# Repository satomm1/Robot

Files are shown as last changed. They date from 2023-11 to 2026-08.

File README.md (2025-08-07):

# Mobile Robot
This repository contains many instructions for setting up and constructing the robot. However, for a comprehensive guide, please visit: [https://satomm1.github.io/mattbot/instructions.html](https://satomm1.github.io/mattbot/index.html).

## Authors
Matthew Sato and Kincho Law<br>
satomm@stanford.edu<br>
Stanford University Department of Civil and Environmental Engineering<br>
Engineering Informatics Lab

## Description
This repo contains mechanical (CAD) designs, electrical schematics, and software for creating a wheeled mobile robot.

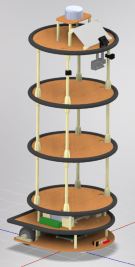
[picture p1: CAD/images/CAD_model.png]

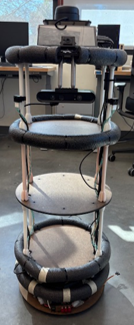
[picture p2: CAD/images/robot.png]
Mobile Robot


- The mechanical design is provided in the `./CAD` directory. In this directory, you will find [detailed instructions](./CAD/README.md) for constructing the mobile robot along with relevant STL/DXF files and a bill of materials. The CAD files were generated in Inventor.
- The electrical design for the various components are located in the `./Electrical` directory. In this directory, you will find electrical schematics and the PCB design for the main control board, IMU breakout board, microphone breakout board, and microphone controller board. A [detailed list of the components and instructions](./Electrical/README.md) for each of these boards is included.
- The software design for the main control board is in the `./Software` directory. This software is for the PIC32 located on the main control board and facilitates communication between the PIC32 and Jetson, performs PID control, odometry, etc. Additionally, the software for the microphone control board is included in this directory. Please visit the [README](./Software/README.md) for more detailed instructions.
- Instructions for the Nvidia Jetson Orin Nano aare provided in the `./Jetson` directory. This directory includes instructions for bringing up the Jetson, setting up the WiFi mesh node connectivity, setting up the Docker environments, and setting up the ROS environment/software stack. Please visit the [Jetson README](./Jetson/README.md) for more details.

## License

This project is licensed under the MIT License - see the [LICENSE](LICENSE) file for details.

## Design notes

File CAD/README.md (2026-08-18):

# CAD

This directory contains the CAD files for the mobile robot. The components for all parts are modeled with Autodesk Inventor and are available in the `Inventor` directory. An older version of the mobile robot design in SolidWorks is available in the `mechanical` zip file.

The remainder of this README provides instructions for creating the mechanical form of the mobile robot for the approximately 1 meter tall robot:

<p align="center">

Mobile Robot CAD Model
Real Mobile Robot
</p>

A comprehensive parts list is located in `BOM.xlsx` that will be needed for constructing this mobile robot.

1) **Laser cut the platforms out of a thin, stiff wood.** I use tempered hardwood (Duron) of 1/8"-1/4" thickness. Every file that should be laser cut is listed in the [Laser_Cuts.md](./Laser_Cuts.md) file. The corresponding DXF files needed for laser cutting are located in the [./dxf](./dxf) directory. For reference, to make sure the files are the correct size/units, the diameter of the circular platforms is 354 mm (14 inches).
2) **Prepare the 3D printed parts.** 3D Print the required parts using PLA plastic. Every file that should be 3D printed is listed in the [3D_prints.md](./3D_prints.md) file. The corresponding STL files are located in the [./stl](./stl/) directory. To verify that the 3D printed parts are the correct size/units, the length of the bearing blocks should be 3 inches (76 mm).

> [!NOTE]
> If you use different components (motor, wheels, etc), the laser cut or 3D printed files may need to be modified first. 

> [!IMPORTANT]
> The height of the motor holders and bearing blocks must be adjusted so that the bottom of the wheels are in plane with the ball casters. Adjust the hardboard_thickness in `Inventor/parameters.xlsx` and update the Inventor model. Verify everything is correct and re-export the motor holders and bearing block stl files.

> [!IMPORTANT]
> You should print the correct bearing block depending on whether your ball bearings have flanges. If the bearings don't have flanges, 3D print the bearing block designated with "no_flange."

3) **Insert heat set inserts.** Use a soldering iron to insert the heat set inserts into any 3D printed part that requires heat set inserts. The small end of the heat  set insert should enter the 3D printed part first. I recommend using a low temperature (~400F or 200C). 

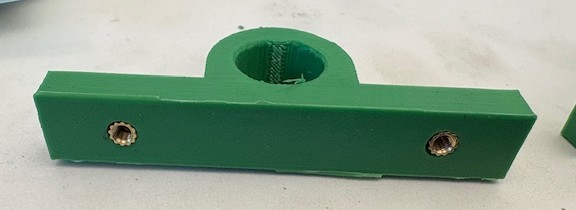
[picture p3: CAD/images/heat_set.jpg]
Heat set inserts


> [!TIP]
> IF you are not familiar with installing heat set inserts, watch this quick video: https://youtu.be/P7nHyI1TwKY?t=189.

4) **Install the motors.** Insert the motors into the motor blocks and secure with screws. **Important**: select the proper length screw (not too long!!!) so that the screw does not go too far and break the motor.

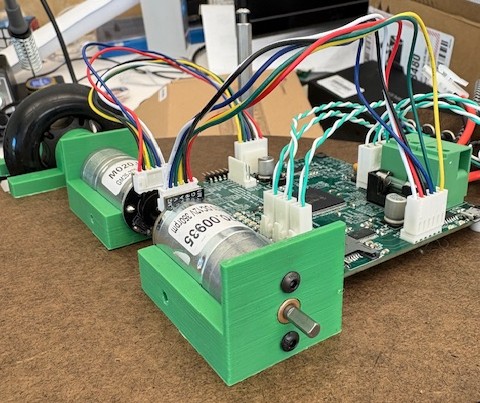
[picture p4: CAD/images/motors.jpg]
Motor Blocks


5) **Install the bearing blocks.** Insert the ball bearings into the bearing blocks (one bearing per bearing block). They are meant to be press fit, but if they are loose then use some epoxy to secure the ball bearings.

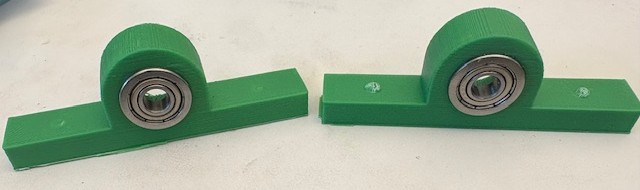
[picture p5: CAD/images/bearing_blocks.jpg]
Bearing Blocks


6) **Install the wheel blocks.** These wheel blocks must be inserted in the wheel to hold the drive shaft. Use epoxy to secure the blocks into the wheel (insert a block on both sides of the wheel-2 total per wheel). Insert the shaft to ensure the blocks are aligned.

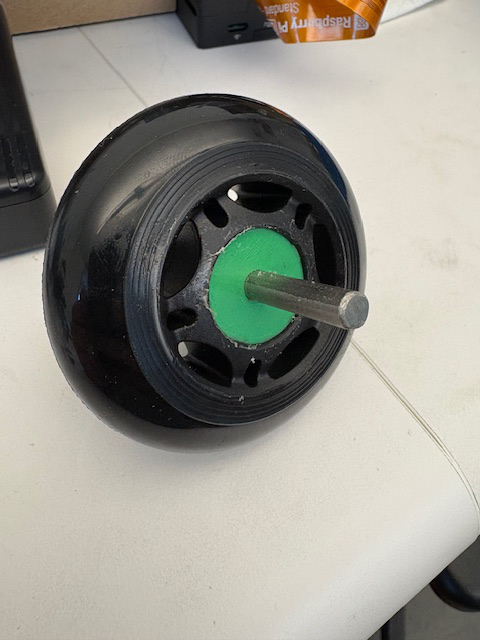
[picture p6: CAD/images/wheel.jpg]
Wheel


7) **(Optional) Install the treaded wheels.** These 3D printed wheel treads can be slipped over the existing skate wheels to provide extra traction (good for carpet).
    - Print the tread shell in PLA (or another hard plastic). The STL is located at [`./stl/pla_wheel_shell_81.5_od_2_thickness.stl`](./stl/pla_wheel_shell_81.5_od_2_thickness.stl). This is meant to slip over 80 mm diameter skate wheels. Fit may vary depending on your skate wheel model. It is a friction fit, so it may be tough to slide over the wheels.
    - Print the wheel treads using TPU (choose your desired TPU hardness; I use 85A). The treads are located at [`./stl/ridge_treads_tpu.stl`](./stl/ridge_treads_tpu.stl). Slide the TPU treads over the shell. I recommend using some glue to attach the TPU treads to the wheel shell.

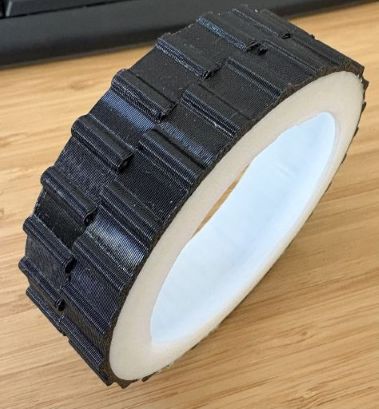
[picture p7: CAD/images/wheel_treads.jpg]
Treaded Wheel


8) **Install all parts on the first platform layer.** 
    - Secure the motor, wheel, bearing blocks, shaft, and spider coupler to the first platform layer. Use M3 screws. The ball bearing should be facing the wheel.
    - Secure the two ball casters to the bottom of the first level using (2) M3 screws per caster.

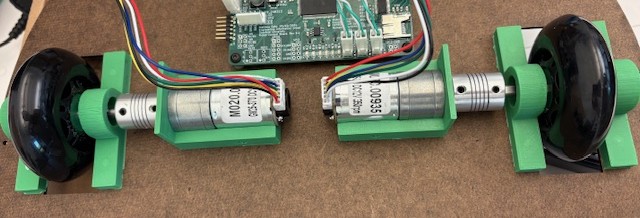
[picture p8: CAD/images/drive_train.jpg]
Drive Train

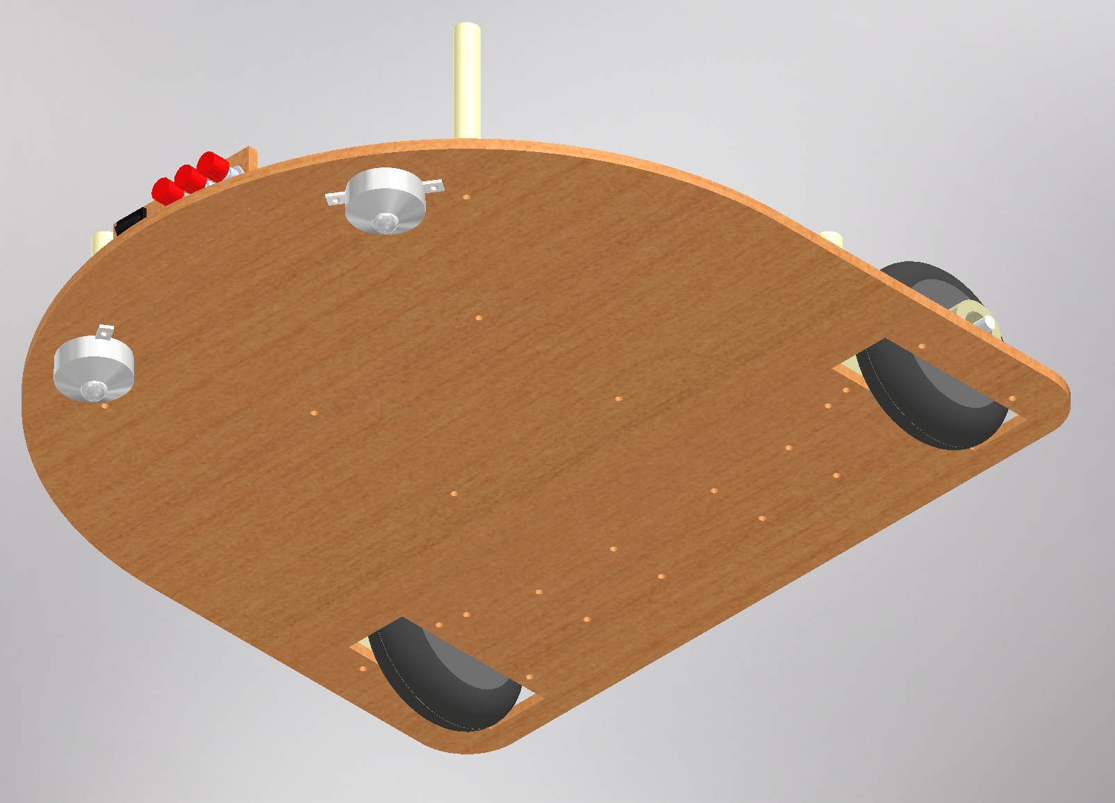
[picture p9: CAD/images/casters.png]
Casters


9) **Install battery holders, Jetson holder, and IMU onto the second level platform.** 

    - Use (16) M3 screws to attach the 2 battery holders and Nvidia Jetson Holder onto the top of the second level platform. 
    - Use (3) M3 screws and plastic standoffs to attach the IMU to the bottom of the second level platform. Please see the [IMU README](../Electrical/IMU_Breakout/README.md) for details on soldering and installing the IMU board.
    - Use (4) M3 screws to attach 3 inch plastic standoffs to the 2nd level platform.

> [!NOTE]
> Use only 3 screws/standoffs for the IMU to prevent unwanted stresses in the IMU!

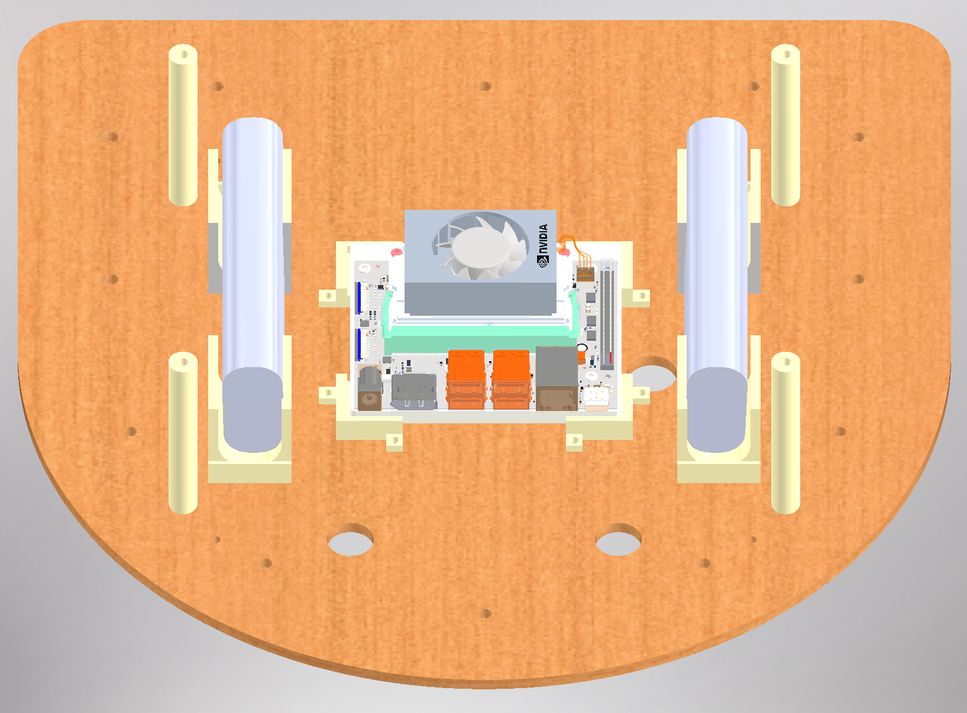
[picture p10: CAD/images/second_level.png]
Second Level Top

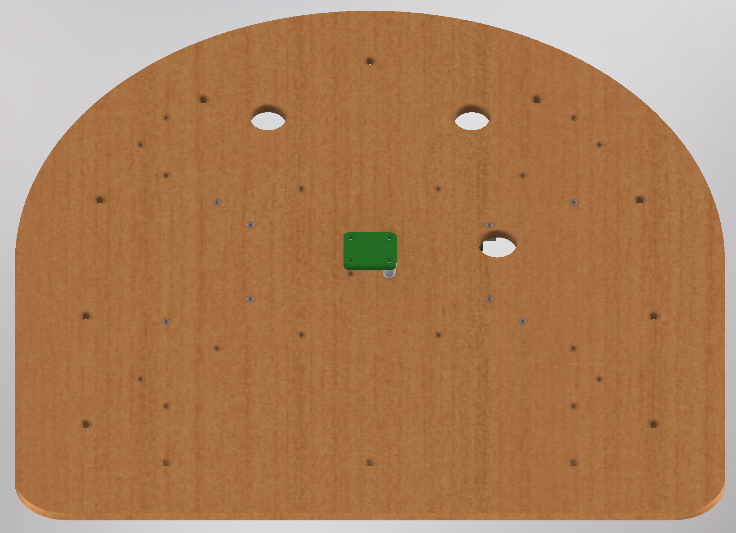
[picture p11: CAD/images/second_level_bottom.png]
Second Level Bottom


10) **Install standoffs on the first layer.** Install the 3 inch standoffs to the first layer platform. Connect the motors and IMU to the PCB, and secure the second layer to the standoffs.

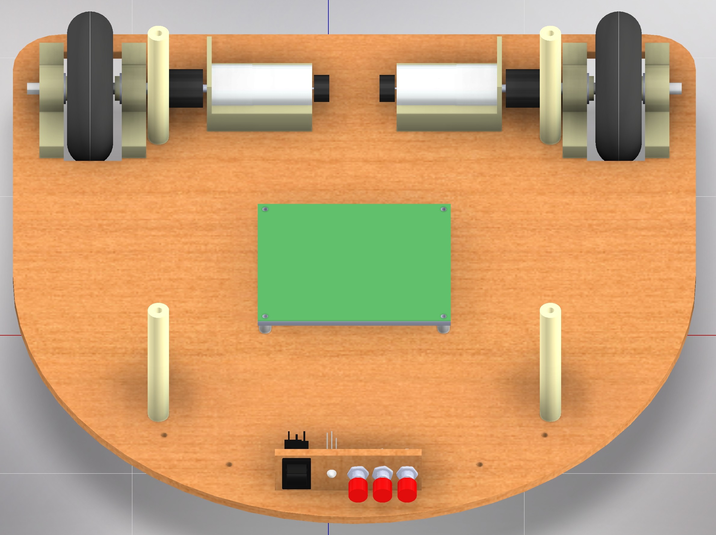
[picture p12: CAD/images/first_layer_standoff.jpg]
First Layer Standoffs


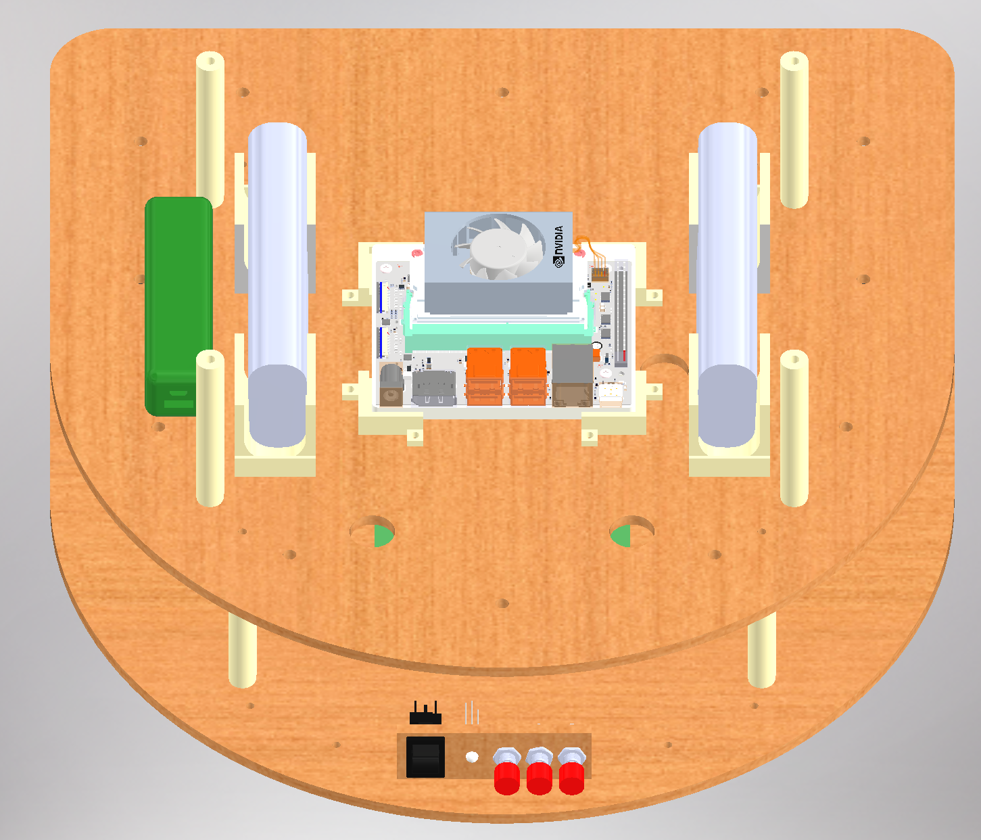
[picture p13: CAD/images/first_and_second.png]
Fist and Second Layer Connected


11) **Secure 3 Pronged standoffs to each platform.** Connect the 3 pronged standoff to the top of levels 3, 4, and 5. This means you will insert (3) M3 screws through the bottom of the platform. Make sure the prongs are aligned so that when you connect the other side they are lined up with the empty holes!

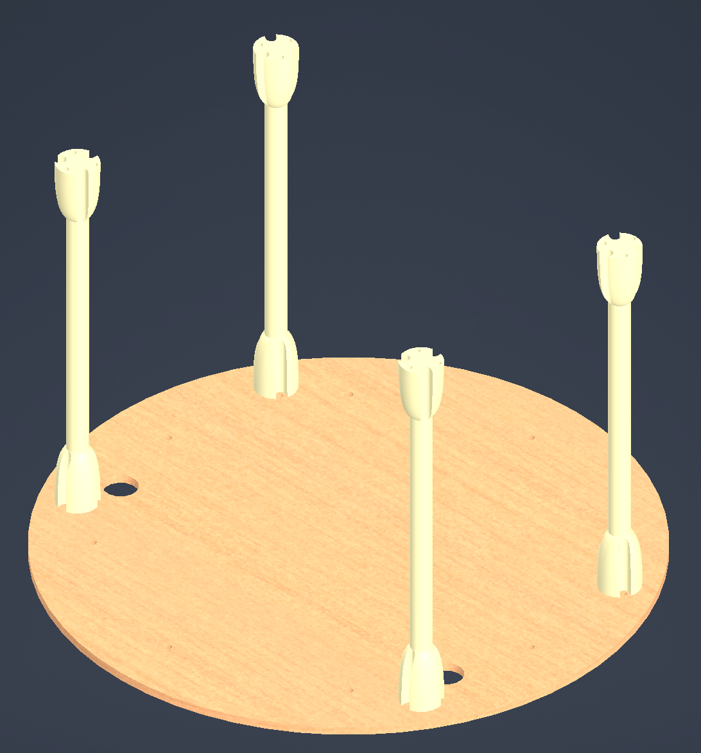
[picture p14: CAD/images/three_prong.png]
Three Prong Standoffs


> [!TIP]
> At this point, I recommend preparing the Jetson and inserting the Jetson into it's platform. Read more instructions [here](../Electrical/README.md) in the `Electrical` directory.

12) **Add Levels 4, 5, and 6.** Add these levels one by one by connecting to the 3 pronged standoffs. This is the most tedious part of the whole process as you will need to attach three M3 screws per standoff. 

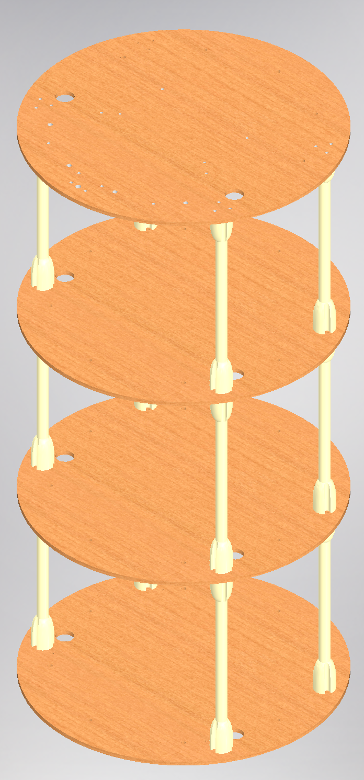
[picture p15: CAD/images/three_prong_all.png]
Three Prong All Connected


13) **Connect the 2nd and 3rd level.** Connect the 2nd and 3rd level using the 3D printed 3 inch standoffs and M3 screws. At this point all the levels are connected!

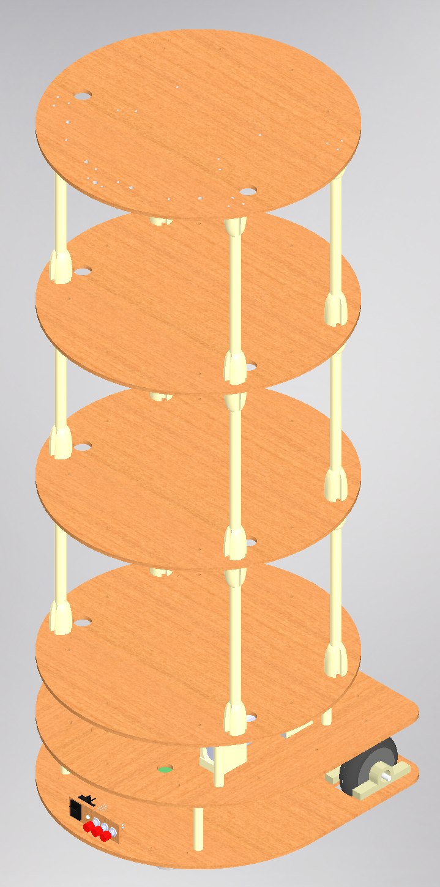
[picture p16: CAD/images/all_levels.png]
All Levels Connected


14) **Attach the LiDAR to the platform and to the top level.** Screw the LiDAR sensor into the platform. Then, attach the LiDAR platform to the top level with the 3.5 inch standoffs. 

> [!IMPORTANT] 
> Do not use too long of screws. 

> [!IMPORTANT]
> The LiDAR cable should be facing the front of the robot.

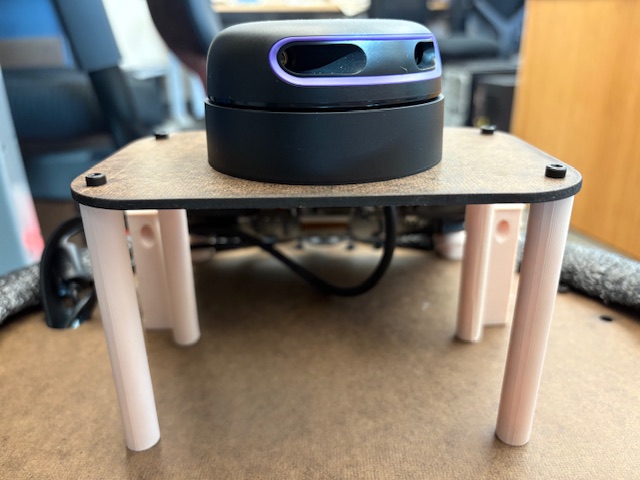
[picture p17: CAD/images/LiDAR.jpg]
LiDAR


15) **Attach the Astra Camera.** Insert the Astra camera into its mount using an M6 screw. Then, attach the mount to the top level using M3 screws.

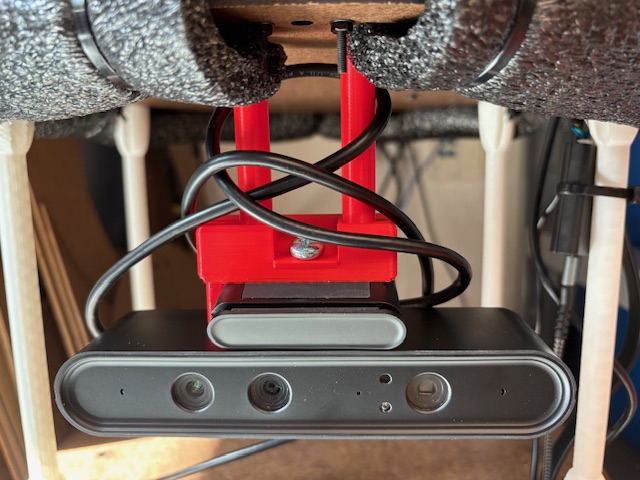
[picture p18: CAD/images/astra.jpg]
Astra Camera


16) **Attach the touch screen.** Attach the touch screen to its legs. The long legs use a screw (provided with the screen) to attach, while the screen just rests in the short legs. Secure the legs to the top platform using M3 screws.

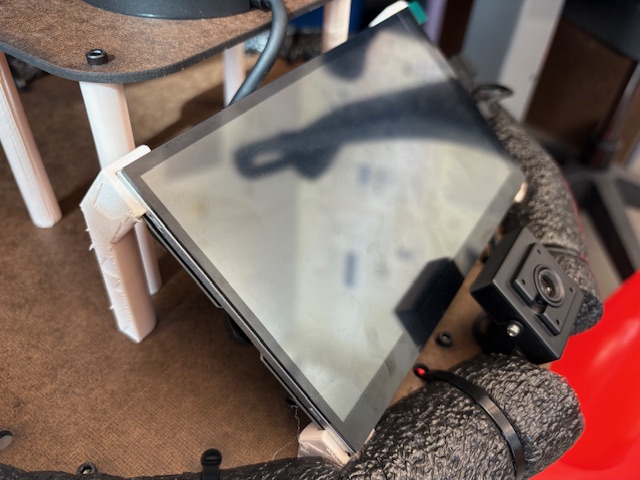
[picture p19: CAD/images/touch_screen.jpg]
Touch Screen


17) **Attach the USB camera.** Use two M3 screws to attach the camera to the top level. 

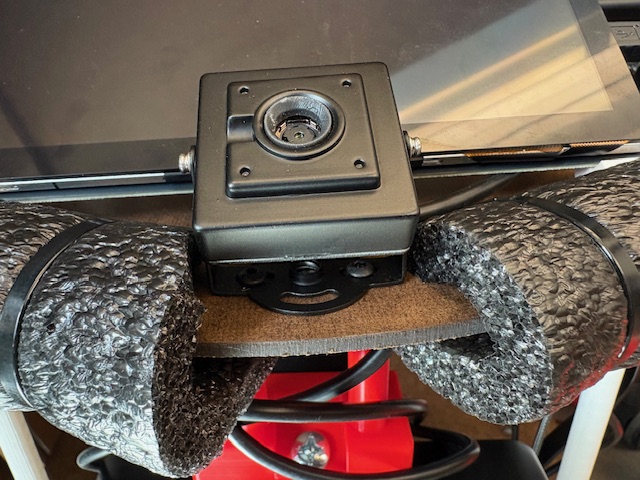
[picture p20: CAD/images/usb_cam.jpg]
USB Camera


18) **Attach the microphones.** 
    - First, the microphones need to be inserted into the housings. To view detailed information on constructing the microphone housing, visit the [microphone README](../Electrical/Microphones/README.md).
    - Second, connect the entire housing to one of the three pronged standoffs using a M3 screw and nut.

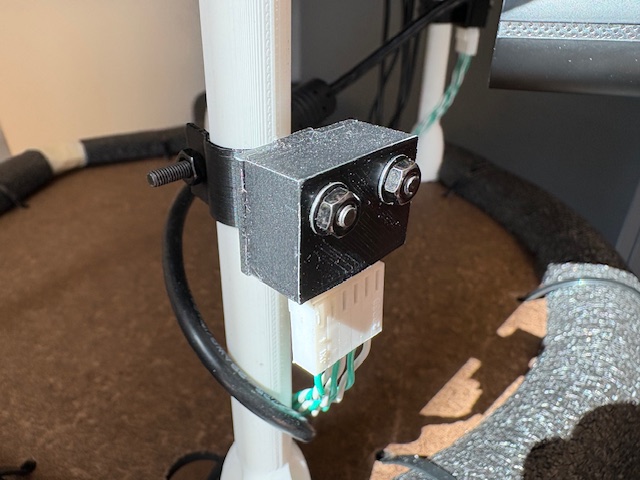
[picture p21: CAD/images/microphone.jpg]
Microphone


19) **Attach the foam bumpers.** Use the zipties to secure the foam bumpers to each level. You may need to cut small sections out of the foam to accomodate the three pronged standoffs. To connect the ends of the foam together, use some masking tape.

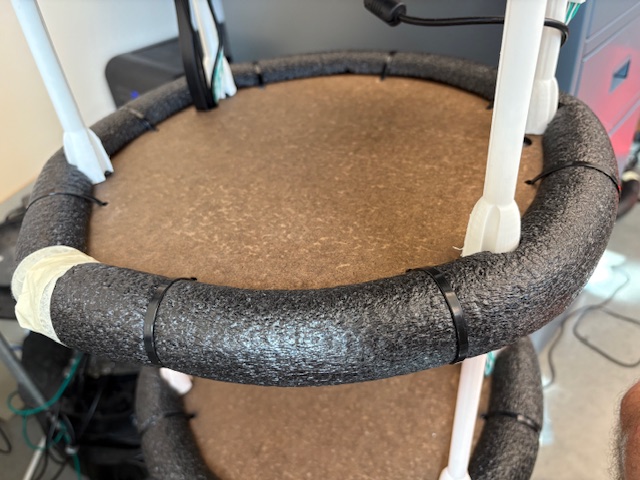
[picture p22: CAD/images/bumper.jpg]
Foam Bumper


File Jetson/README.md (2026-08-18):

# Jetson Instructions

We use an 8 GB Nvidia Jetson Orin Nano Developer Kit for high level control of the mobile robot.

## Jetson Bring Up Instructions
1) Flash a microSD card with the Jetpack Image and insert into the Jetson. I have had WiFi card issues with Jetpack 6.x, so I recommend using Jetpack 5.x (latest version as of May 2025 is 5.1.5). Please find the SD card image at this webpage: https://developer.nvidia.com/embedded/jetpack-sdk-515.

    To flash the SD card, you will need to first format the SD card using: https://www.sdcard.org/downloads/formatter/. Then, use [Balena etcher](https://etcher.balena.io/) to flash the SD card.

    Alternatively, you can use the Nvidia SDK Manager to flash the Jetson. If you have a device that is natively running Ubuntu, this will work great. Otherwise, you will need a VM (specifically VMware Workstation). Some tips if using a VM – make sure you allocate plenty of hard disk memory for the VM and change the settings so that the USB connection to the Jetson automatically is sent to the VM.

2) Switch out the default WiFi card. The default WiFi card does not support roaming (which is necessary to switch between mesh nodes). We use the Intel AC9260 WiFi card. The WiFi card is located on the bottom of the Jetson and can be removed with a screwdriver. 

>[!Important]
>Be sure to reconnect the antennas to the new WiFi card!

3) Power on the device while connected to a monitor. Connect to Wi-Fi so that we can SSH into the device.

4) Call: `sudo apt update`. Then, install nano: `sudo apt install nano`.

5) Set up SPI capabilities on headers pins so that we can communicate with the MCU:
    - Navigate to opt/nvidia/jetson-io: `cd /opt/nvidia/jetson-io`
    - Call `sudo python3 jetson-io.py`
        - We need to manullay conifgure the 40 pin header
        - Select options to activate SPI1, SPI3, and I2S
    - Reboot the Jetson for the new pin functions to take effect

6) Load the spidev module automatically on start up.

    **Automated (recommended):** download and run `spidev_setup.sh` from this directory:

    ```
    cd ~
    wget "https://raw.githubusercontent.com/satomm1/Robot/main/Jetson/spidev_setup.sh"
    chmod +x spidev_setup.sh
    sudo ./spidev_setup.sh
    sudo reboot
    ```

    **Manual:** edit `/etc/modules-load.d/spidev.conf`, write `spidev` in the file, save, and reboot.

7) If you have issues with `dev/ttyUSB0`, you may need to call `sudo apt remove brltty`

8) Connect the corresponding SPI pins on the header to the SPI pins on the MCU control board. The corresponding pins are listed in the [Electrical README](../Electrical/README.md).

9) Connect the corresponding I2S pins on the header to the I2S pins on the microphone control board. The corresponding pins are listed in the [Microphone README](../Electrical/Microphones/README.md).

## WiFi Roaming Setup Instructions

Configuring the WiFi driver to roam is not straightforward. Roaming lets the Jetson switch access points when the signal is weak, instead of waiting for a full disconnect.

We automate setup with `wifi_roaming_setup.sh` in this directory. The script:

1. **NetworkManager** — Writes `/etc/NetworkManager/NetworkManager.conf` so your WiFi NIC (detected as `wlan*`, e.g. `wlan0`) is unmanaged by NetworkManager.
2. **wpa_supplicant** — Writes `/etc/wpa_supplicant/wpa_supplicant-<iface>.conf` with roaming `bgscan`, then enables **`wpa_supplicant@<iface>.service`** as the sole WiFi controller (and disables the generic `wpa_supplicant.service` to avoid conflicts).
3. **DHCP on boot** — Installs `/usr/local/bin/custom_wifi.sh` (runs `dhclient` only) and **`custom_wifi.service`**, which starts after `wpa_supplicant@<iface>`.

In `bgscan="simple:30:-60:600"`: **-60** = -60 dBm to trigger a scan, **30** = scan every 30 seconds while below -60 dBm, **600** = scan every 600 seconds otherwise.

### Prerequisites

1. Install a roaming-capable WiFi card and driver. We use the **Intel AC9260** (see bring-up step 2).
2. Complete initial Jetson bring-up through step 4 (`sudo apt update`, `nano` installed) so you can SSH in.
3. On the Jetson, install `wpasupplicant` if it is not already present:
    ```
    sudo apt install wpasupplicant
    ```
4. Confirm a `wlan*` interface exists (e.g. `wlan0`):
    ```
    ip link show | grep wlan
    ```

### Copy the setup script to the Jetson

**Option A — Download with `wget`**

On the Jetson:

```
cd ~
wget "https://raw.githubusercontent.com/satomm1/Robot/main/Jetson/wifi_roaming_setup.sh"
chmod +x wifi_roaming_setup.sh
```

**Option B — Create the file with `nano`**

On the Jetson, open the file from this repo in a browser or editor, copy its contents, then:

```
nano ~/wifi_roaming_setup.sh
```

Paste the contents, save (`Ctrl+O`, `Enter`, `Ctrl+X`), then:

```
chmod +x ~/wifi_roaming_setup.sh
```

### Run the setup script

SSH into the Jetson, then:

```
chmod +x ~/wifi_roaming_setup.sh
sudo ~/wifi_roaming_setup.sh
```

The script will:

- Prompt for confirmation (it modifies system network files; backups use a `.bak` suffix).
- Auto-detect the first `wlan*` interface and its MAC address.
- Prompt for your WiFi **SSID** and **password**.
- Ask whether the device operates in the **USA** (`US`) or **South Korea** (`KR`) and set the WiFi regulatory country code accordingly.

When it finishes, **reboot**:

```
sudo reboot
```

### Verify after reboot

```
sudo systemctl status wpa_supplicant@wlan0 custom_wifi.service
iw dev wlan0 link
ip addr show wlan0
```

Replace `wlan0` with your interface name if different.

Optional manual test before reboot:

```
sudo systemctl start custom_wifi.service
```

### Undo / restore previous networking

If you need to revert:

```
sudo systemctl disable --now custom_wifi.service
sudo systemctl disable --now wpa_supplicant@wlan0.service
sudo systemctl enable wpa_supplicant.service
sudo rm /etc/systemd/system/custom_wifi.service /usr/local/bin/custom_wifi.sh
sudo mv /etc/wpa_supplicant/wpa_supplicant-wlan0.conf.bak /etc/wpa_supplicant/wpa_supplicant-wlan0.conf
sudo mv /etc/NetworkManager/NetworkManager.conf.bak /etc/NetworkManager/NetworkManager.conf
sudo reboot
```

Adjust paths if your interface is not `wlan0` or if no `.bak` files were created.

> [!TIP]
> Assign a fixed IP to the Jetson’s WiFi MAC in your router’s DHCP settings so the Jetson keeps the same address on the LAN.

## Docker Setup

1)  Follow system setup (through at least the “Relocating Docker Data Root” step) from https://github.com/dusty-nv/jetson-containers/blob/master/docs/setup.md
    
    If you have NVME storage to add, I found this tutorial helpful for setting up the NVME storage: https://www.digitalocean.com/community/tutorials/how-to-partition-and-format-storage-devices-in-linux

	Also, be sure to add the following line to `etc/docker/daemon.json`:
    ```
	"data-root": "/mnt/data"
    ```

	Note: `/data` should be whatever your mount folder name is…

    Then, restart docker:
    ```
    sudo systemctl restart docker
    ```

----

### Pull the pre-built `ml_ros` image (recommended)

Most setups should use the pre-built **`ml_ros`** image from GitHub Container Registry (GHCR). Building the image from scratch on the Jetson is only needed if you are customizing the container; see [BUILD_ML_ROS.md](BUILD_ML_ROS.md).

After Docker is installed on the Jetson, pull the published image from GHCR:

```bash
docker pull ghcr.io/satomm1/ml_ros:latest
```

Verify:

```bash
docker images ghcr.io/satomm1/ml_ros:latest
```

No `docker login` is required—the package is public on GHCR.

To refresh an existing Jetson after the image is updated on GHCR, run `docker pull ghcr.io/satomm1/ml_ros:latest` again.

Then continue with [Setting Up ROS Workspace](#setting-up-ros-workspace).

**Offline / no registry access:** on a connected machine, `docker pull ghcr.io/satomm1/ml_ros:latest`, then `docker save ghcr.io/satomm1/ml_ros:latest | gzip > ml_ros.tar.gz`, copy to the Jetson, and `sudo docker load < ml_ros.tar.gz`.

----

### Setting Up ROS Workspace
1) Start the ROS docker container. 
    ```
    sudo docker run --runtime nvidia --network=host -v ~/workspaces/catkin_ws:/workspace/catkin_ws -v ~/gemini_api:/gemini_code -v /dev/bus/usb:/dev/bus/usb -v /dev/video0:/dev/video0 -v /dev/video1:/dev/video1 -it --device=/dev/ttyUSB0 --device=/dev/spidev0.0 --rm --privileged --name ros_noetic ghcr.io/satomm1/ml_ros:latest
    ```

    You should source ROS via:
    ```
    source /opt/ros/noetic/setup.bash
    ```

    Within the docker container, navigate to `/workspace/catkin_ws` (you may need to create this directory):
    ```
    cd /workspace/catkin_ws
    ```

2) Now, create the devel and src directories:
    ```
    mkdir devel src
    ```

3) Now, build the workspace:
    ```
    catkin_make
    ```

4) Source the build and go to the `src` directory:
    ```
    source devel/setup.bash
	cd src
    ```

5) Now, clone the following repositories and switch to the noetic branch. To make cloning easier, I have provided a script to automatically clone all the relevant repositories and a few useful files. Copy the `clone_repos.sh` script to your Jetson, make it executable, and then run the script:
    ```
	nano clone_repos.sh
	(copy clone_repos.sh code here)
	ctrl+x, y (to save file)
	chmod +x clone_repos.sh
	. clone_repos.sh
    ```

    The script will clone the following repositories/files from https://github.com/satomm1/
    
    - mattbot_record
    - mattbot_capture
    - mattbot_bringup          
    - mattbot_dds         
    - mattbot_image_detection  
    - mattbot_mcl              
    - mattbot_navigation	 
    - mattbot_teleop
    - ros_astra_camera
    - rplidar_ros
    - twist_mux
    - slam_gmapping
    - robot_env.sh (From this repo)
    - startup_script.py (from this repo)

6) Navigate back to the `catkin_ws` directory and build the packages:
    ```
	cd /workspace/catkin_ws
	catkin_make
	source devel/setup.bash
    ```

7) Add important information to the `robot_env.sh` file:
    ```
    nano /workspace/catkin_ws/src/robot_env.sh
    ```
    Please update the file with the Jetson IP address, Robot ID, MCU SPI number, camera type, and robot height.

8) Configure Cyclone DDS peer discovery in `cyclonedds.xml` (downloaded by `clone_repos.sh` in step 5):
    ```
    nano /workspace/catkin_ws/src/cyclonedds.xml
    ```
    This file disables multicast and uses an explicit peer list for WiFi mesh discovery. **You must update the `<Peer Address="..."/>` entries** so they list the actual IP addresses of every robot and device that should participate in DDS discovery on your network.

    - Include this Jetson’s IP address (the same value you set for `ROS_IP` in `robot_env.sh`).
    - Add the IP addresses of any other robots or machines running ROS on the mesh.
    - Remove any placeholder entries that do not correspond to a real device.

    The default file assumes the `wlan0` interface; change `<NetworkInterface name="wlan0"/>` only if your WiFi interface has a different name.

9) Make sure our ROS environment and robot environment settings are sourced via the `bashrc` file:
    ```
	nano ~/.bashrc
    ```
    Append the following:
    ```
    source /workspace/catkin_ws/devel/setup.bash
    source /workspace/catkin_ws/src/robot_env.sh
    ```
    Source the bashrc file:
    ```
    source ~/.bashrc
    ```

10) Test the setup, call roscore. If you have no errors, this is good!
    ```
	roscore 
    ```

11) Set up the Astra Camera.  You will also need to navigate to the `ros_astra_camera` directory and perform these two commands outside of the docker container:
    ```
    cd ~/workspaces/catkin_ws/src/ros_astra_camera
    ./scripts/create_udev_rules
    sudo udevadm control --reload && sudo udevadm trigger
    ```

12) You should commit the docker container to save any changes. Outside of the docker container (but with the docker container running), run this command:
    ```
    sudo docker commit ros_noetic ml_ros:latest
    ```

----
### Setting up the Gemini Container

1) Pull the Gemini image from GHCR (public; no `docker login` required):

    ```
    docker pull ghcr.io/satomm1/gemini:latest
    ```

    To refresh after an update on GHCR, run `docker pull ghcr.io/satomm1/gemini:latest` again.

    **Offline / no registry access:** on a connected machine, `docker pull ghcr.io/satomm1/gemini:latest`, then `docker save ghcr.io/satomm1/gemini:latest | gzip > gemini.tar.gz`, copy to the Jetson, and `sudo docker load < gemini.tar.gz`.

2) Clone the gemini_api repo:
    ```
    cd ~ && git clone https://github.com/satomm1/gemini_api.git
    ```

3) Start the container:
    ```
    sudo docker run -v ~/gemini_api:/gemini_code -w /gemini_code -it --rm --privileged -p 5000:5000 --name gemini ghcr.io/satomm1/gemini:latest
    ```

    Speech is handled by the display app on the Jetson host (Piper TTS), so this container does not need an audio volume.

4) To run the needed file, run the `start_scripts.sh` script (which just runs `endpoint.py`):
    ```
    . start_scripts.sh
    ```

----
## Jetson host service (GUI startup)

The operator GUI uses HTTP on port **8081** on the Jetson host (outside Docker) to start/stop the ROS container and power off the machine. ROS launch and software updates stay on port **8080** inside Docker (`startup_script.py`).

**Automated (recommended):** after Docker is installed, run `jetson-host-install.sh` from this directory. Full details: [JETSON_HOST_SERVICE.md](JETSON_HOST_SERVICE.md).

```
cd ~
wget "https://raw.githubusercontent.com/satomm1/Robot/main/Jetson/jetson-host-install.sh"
chmod +x jetson-host-install.sh
sudo ./jetson-host-install.sh
```

Verify: `curl -s http://127.0.0.1:8081/status`

----
### Setting up the Display

The touch-screen display runs on the Jetson host (outside Docker). It shows messages sent to `localhost:65432` and speaks them with [Piper TTS](https://github.com/rhasspy/piper). There is **no PyInstaller executable** — a user systemd service runs `display_app.py` directly from the cloned repo.

Install the [Jetson host service](#jetson-host-service-gui-startup) first so the toolbar **Start Docker** / **Start Robot** / **Stop Robot** buttons work.

1) Clone the display repository:
    ```
    cd ~
    git clone https://github.com/satomm1/mattbot_display.git
    cd mattbot_display
    ```

2) Install as a user systemd service (recommended). This installs `python3-tk` and `alsa-utils`, downloads Piper TTS into `./piper/`, enables `mattbot-display`, and adds a desktop shortcut:
    ```
    chmod +x scripts/install.sh
    sudo ./scripts/install.sh
    ```
    The service runs the code in this clone. After you edit `display_app.py`, restart from the desktop — no rebuild or copy step.

3) After a desktop login, the display should start automatically. To start it manually, double-click **Start-Mattbot-Display.sh** on the desktop, or:
    ```
    systemctl --user start mattbot-display
    ```
    Status and logs:
    ```
    systemctl --user status mattbot-display
    journalctl --user -u mattbot-display -n 30
    ```
    If you see `couldn't connect to display ":0"`, log in to the desktop first, then `systemctl --user restart mattbot-display`. Auto-login is recommended for kiosk use.

4) To test without systemd:
    ```
    python3 display_app.py
    ```
    Messages sent to `localhost:65432` appear on screen and are spoken (status lines like `Listening...` are shown but not spoken). HDMI audio is auto-detected from `aplay -l`. To force a device, set `MATTBOT_ALSA_DEVICE` (e.g. `plughw:2,3`).

5) Daily use:
    - **Exit** on the display returns you to the desktop (the service stops and does not auto-restart on a clean exit).
    - Double-click **Start-Mattbot-Display.sh** to start it again.
    - On LXDE / PCManFM, if the shortcut opens in a text editor, choose **Execute** / **Run**, or set PCManFM **Edit → Preferences → General → “Don’t ask options on launch executable file”**.

You do **not** need `~/Desktop/audio/` or MP3 files. Full details (env vars, socket protocol, troubleshooting): https://github.com/satomm1/mattbot_display

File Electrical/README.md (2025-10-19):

# Electrical

Contains the electrical schematics and PCB gerber files for the Robot electronics. There are several Schematics/PCB designs for a variety of uses:
- Main Board - the main motor controller and communicator with the Jetson
- Microphone - a breakout board for a Mems omnidirectional microphone
- IMU Breakout - a breakout board containing a 6-axis IMU
- Reflective Sensor - a breakout board containing a sensor for very short distance measurements

The Main Board is the only required electronics, so start here. The others (IMU, reflective, microphone) provide additional functionality should you wish to include them.

## Ordering a Manufactured PCB Board
You can use a variety of vendors to order a PCB. I have used JLPCB in the past. To order, all you need to do is submit the zipped `gerber_files` folder to the vendor.

## Main Board
The [main board](./MainBoard/) contains the PIC32 MCU, motor drivers, power supply, button sensors, Jetson communications, etc. In this directory, you will find a comprehensive schematic and PCB layout, as well as ready to use Gerber files for PCB manufacturing.

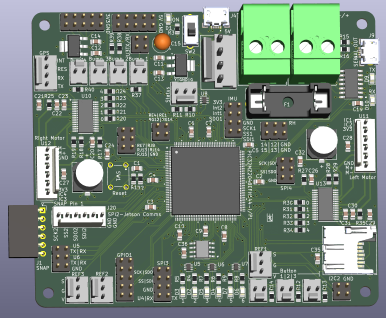
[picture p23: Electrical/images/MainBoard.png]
Main Board


After populating the board, we need to make several connections from the board to other components of the mobile robot:

1. Connecting to the motors

    - The motors should be connected to the motor terminals via a 6 position female molex connector. Insert the wires corresponding to the markings on the PCB silkscreen.

2. Connecting to the Jetson

    - The jetson is connected via a 6 position female molex connector on the PCB, and dupont connectors on the Jetson header. Only the first five positions on the PCB need to be connected (SCK, SS, SDO, SDI, GND) and must be matched to the corresponding SPI pins on the Jetson header. For example, if using SPI1 (SPI3) on the jetson:

        | Jetson Pin Name       | Jetson GPIO | PCB Pin Name |
        |-----------------------|-------------|--------------|
        | SPI1_SCLK (SPI3_SCLK) | 23 (13)     | SCK          |
        | SPI1_CS0 (SPI3_CS0)   | 24 (18)     | SS           |
        | SPI1_din (SPI3_din)   | 21 (22)     | SDO          |
        | SPI1_dout (SPI3_dout) | 19 (37)     | SDI          |
        | GND                   | 25 (20)     | GND          |

    - **Note:** If using twisted pair wire, **DO NOT** twist the SDO and SDI wires together. This will lead to unintended crosstalk that can significantly degrade the ability of the Jetson to communicate with the PCB.

3. Connecting to the power supply
    
    - Insert the Tamiya style leads for the NiMH batteries into the tall power blocks. The positive (red) and negative (black) terminals are indicated on the PCB via +/- silkscreen. 
    - Connect to the main power switch. The rocker switch should be connected to the 4 position Molex terminal near the battery terminals. Solder four wires to the rocker switch (with heat shrink tubing to protect the connection) and connect the other four ends to the corresponding female molex connector. The positions are as follows:

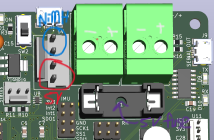
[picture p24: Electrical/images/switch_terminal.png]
Power Terminals
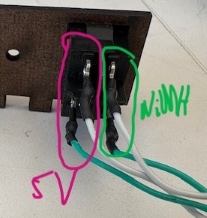
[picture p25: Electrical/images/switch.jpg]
Switch
         

    - Insert a 5A fuse into the fuse holder.
    - Insert the micro-usb cable for the 5V battery into the port at the front of the board (the other micro-usb port is used for serial debugging)
    - Now, you can power on the PCB with the rocker switch. Alternatively, the small switch on the PCB is used to provide only 5V power supply access to the board in case you do not need to run the motors.

4. Connecting to the buttons
    
    - Solder a pair of wires to each button (with heat shrink tubing to protect the cunnection) and connect the other ends of the wire to a 2-position female molex connector.

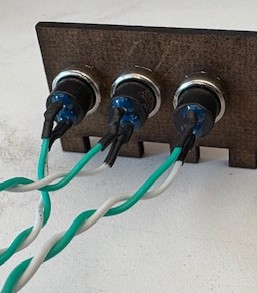
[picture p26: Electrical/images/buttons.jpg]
Buttons
        

## Microphone

For detailed instructions on the Microphone, visit the [Microphone README Page](./Microphones/README.md).

## IMU Breakout
For detailed instructions on the IMU, visit the [IMU README Page](./IMU_Breakout/README.md).

## Reflective Sensor

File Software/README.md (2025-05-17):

# Software

This directory containts the software for the microcontroller and instructions for setting up the Nvidia Jetson Orin Nano.

## Microcontroller Software
The microcontroller software provides the following functionality:
- PID motor control
- Odometry calculations
- Communication with the Nvidia Jetson via SPI
- Button sensing 
- Options for memory writing/reading with on board EEPROM and micro-SD
- Option to connect an IMU

To program the microcontroller, you will need to 1) download/install the MPLAB IDE from Microchip and 2) download/install the MPBLAB XC32 compiler from Microchip. You will also need a MPLAB programming device. I use the MPLAB Snap In-Circuit Debugger and Programmer, which provides the needed functionality and is affordable.

To program the PIC32, ensure the power supply is turned on and the SNAP programmer is connected. Open MPLAB and open the project located in the `./MCU` directory. Open the `FrameworkHeaders/ES_Configure.h` file and select the `ROBOT_ID`. If you are using a different PCB revision or motor type, you may need to modify `PCB_REV` and `MOTOR_TYPE`. If the motor type does not fit one of the predefined versions, you will need to modify the `Source  Files/MotorSM.c` file.

Then, program the device by pressing the 'Make and Program Device' button at the top of MPLAB:

Make and Program Button

To verify the successful programming of the PIC32, you can connect to the board via micro USB. Communicate with the PIC32 via serial port with baud rate 115200 using something such as TeraTerm.

## Setting up the Jetson
Second, this directory provides information for setting the Nvidia Jetson Orin Nano device. Included in this directory is a word document describing:
1) How to bring up the Jetson
2) How to set up the necessary Docker container on the Jetson
3) How to set up Wi-Fi on the Jetson to allow roaming

Please follow these instructions for successful setup of the Jetson device.

The ROS repos that are run on the Jetson are located in other git repos that can be found on [my GitHub profile](https://github.com/satomm1).

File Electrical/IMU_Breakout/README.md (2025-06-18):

# 6-axis IMU

This directory contains the electrical schematic for a breakout board for the Bosch BMI323 6-axis IMU. This IMU provides a 16 bit digital triaxial accelerometer, a 16 bit digital triaxial gyroscope, and a 16 bit digital temperature sensor.

This breakout board is designed so that the IMU can be placed anywhere that is convenient.

## Soldering the IMU
This IMU is in a QFN package, which means the device should be reflow soldered. Alternatively, you can carefully apply solder to the PCB pads, put the IMU on top, and use a heat gun to solder the IMU.

## Pin directions
The header pins should be soldered on the bottom of the PCB:

IMU Breakout Board

## Installing the IMU
The assembly is meant to be installed on the robot with the IMU facing upwards. The positive X/Y/Z axes are designated on the board. The IMU should be connected via wire to the designated header on the main control board:

| IMU Breakout Pin | Main Control Board Connection |
|---|---|
| 3V3 | 3.3V |
| GND | GND |
| SCK | SCK |
| CS | CS |
| SDO | SDI |
| SDI | SDO |
| INT1 | INT1 (Currently Unused) |
| INT2 | INT2 (Currently Unused) |

The IMU connection on the main control board is indicated below:

Main Board with IMU Pins Highlighted

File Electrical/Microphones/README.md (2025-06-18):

# Microphone Design

This directory holds the electrical design for the microphones. Note, you will need one  PIC32 board and two microphone boards for a single system. The two microphones allows for stereo audio. The PIC32 board is an intermediary that translates the audio signal into a format that the Jetson can read.

> [!WARNING] 
> Soldering the microphones is not easy. You will need solder paste and a reflow oven.  You can order a stencil for the solder paste, or manually apply the solder paste to the microphone pads (be careful not to add too much solder!).

> [!TIP]
> Make sure to solder the 6 pin right angle connector in the correct direction. See picture below for guidance.

## Putting the Microphones Together
Once you have a soldered microphone PCB, we can construct the full microphone in its housing. 3D print the housings (instructions in the [Mechanical Directory](../../CAD/README.md)). For a more robust microphone, we use a gasket and an acoustically transparent fabric to prevent debris from entering the microphone port. To construct the housing

1. Attach the gasket, making a hole slightly larger than the microphone port (be sure the hole is big enough even after the gasket is compressed). For the gasket, I use a foam-like double sided tape.

    Gasket 

2. Place the acoustically transparent membrane over the gasket and PCB, cut holes for the screws. For the acoustically transparent fabric, I use Muslin (which can be picked up at your local fabric store).

    Acoustically Transparent Membrane

3. Attach the PCB to the 3D printed housing using two screws.

    Housing Front  Housing Back 

4. Connect the two microphones to the PIC32 Control Board using Molex Connectors.

    PIC32 Board

## Setting up the PIC32
Once you have a soldered PIC32, you must program it with the source code located in the [PIC32 Firmware](./PIC32%20Firmware/) directory. Connect the two microphones to the PIC32 board. Connect the PIC32 board to the Jetson's I2S pins. Then, follow the instructions at https://github.com/satomm1/mattbot_record/tree/noetic for Jetson software.

## PIC32 to Jetson I2S Pin Mapping

We will be using the 6-pin connector for this microphone (ignore the 5 pin header). Make sure the switch is switched in the upward position. Then, connect the pins on the PIC32 Board to the Jetson using the following connections (may need to adjust pin # based on your hardware):

| PIC32 Pin | Jetson I2S Pin | Jetson I2S Pin Number |
|---|---|---|
| CS | I2S2_FS | 35 |
| SDI | I2S2_DOUT | 40 |
| SDO | I2S2_DIN | 38 |
| SCK | I2S2_SCLK | 12 |
| GND | GND | 14 |
| 3V3 | 3.3V | 17 |

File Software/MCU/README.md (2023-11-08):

# MCU Software

Contains the software for the low level microcontroller. Handles reading of sensors and communicating.

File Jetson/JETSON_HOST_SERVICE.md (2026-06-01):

# Jetson host service (port 8081)

The GUI Robot Startup panel (in [dds_robot_platform](https://github.com/satomm1/dds_robot_platform)) talks to a small HTTP service on the **Jetson base machine** (not inside Docker) for Docker start/stop and power off. ROS launch remains on port **8080** inside the `ros_noetic` container (`startup_script.py`).

You do **not** need to clone the GUI repo on the Jetson. Copy one install script from this repo and run it.

## Install

From your development machine (paths relative to this Robot repo):

```bash
scp Jetson/jetson-host-install.sh YOUR_USER@JETSON_IP:~/
ssh YOUR_USER@JETSON_IP 'sudo bash ~/jetson-host-install.sh'
```

Or download on the Jetson:

```bash
cd ~
wget "https://raw.githubusercontent.com/satomm1/Robot/main/Jetson/jetson-host-install.sh"
chmod +x jetson-host-install.sh
sudo ./jetson-host-install.sh
```

If you see `/usr/bin/env: 'bash\r': No such file or directory`, the file has Windows (CRLF) line endings. On the Jetson run `sed -i 's/\r$//' ~/jetson-host-install.sh` and run again, or re-`scp` from a checkout that uses LF for `*.sh` (see repo `.gitattributes`).

The installer writes:

| Path | Purpose |
|---|---|
| `/opt/robot/host_service.py` | HTTP service (defaults baked in; home dir set at install) |
| `robot-host-service.service` | systemd unit (enabled on boot) |

Re-installing replaces `host_service.py` and restarts the service. To change Docker paths or the `docker run` command, edit `/opt/robot/host_service.py` on the Jetson and run `sudo systemctl restart robot-host-service`.

Verify:

```bash
curl -s http://127.0.0.1:8081/status
# {"host_service": true, "docker_running": false, "container": "ros_noetic"}
```

Open port **8081** from your operator PC if a firewall is enabled.

## Optional: download `host_service.py` from GitHub

```bash
sudo ROBOT_HOST_SERVICE_RAW_URL='https://raw.githubusercontent.com/satomm1/Robot/main/Jetson/host_service.py' \
  bash ~/jetson-host-install.sh
```

The install script still substitutes `__JETSON_HOME__` in `DOCKER_RUN_CMD` after download.

## Endpoints

| GET path | Action |
|---|---|
| `/status` | JSON: host service up, whether `ros_noetic` is running |
| `/docker-start` | Start ROS container (detached `docker run`) |
| `/docker-stop` | Stop `ros_noetic` only |
| `/poweroff` | Stop **all** running containers, then `shutdown -h now` |

## Repo layout (developers)

| File | Role |
|---|---|
| `jetson-host-install.sh` | **Ship this to the Jetson** — self-contained installer |
| `host_service.py` | Source of truth; keep in sync with embedded copy in install script |
| `robot-host-service.service` | Reference systemd unit (also embedded in install script) |

After editing `host_service.py` in the repo, update the embedded heredoc in `jetson-host-install.sh` before deploying to robots.

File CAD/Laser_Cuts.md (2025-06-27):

# Components to be Laser Cut

A laser cutter is used to produce the platforms of the mobile robot. Please visit the `dxf` directory to obtain these files. For full construction instructions, visit the [Mechanical README](./README.md).

> [!NOTE] 
> Some of these dxf files may need to be modified depending on your design (i.e., size/shape of robot).

Here at Stanford, a Trotec SP500 (Lab64) or Universal Laser Systems VLS 4.60 (PRL AMPS) laser cutter is used. Any laser cutter can be used, as long as the laser cutter supports the size of the parts and the materials.

## Laser Cut Parts List
The table below contains all the parts to be laser cut. 

### Materials
We use a tempered hardboard for the material, such as [this product available at Home Depot](https://www.homedepot.com/p/Hardboard-Tempered-Panel-Common-3-16-in-x-4-ft-x-8-ft-Actual-0-175-in-x-48-in-x-96-in-832780/202404545). Typically, we use between 1/8 to 1/4 inch thick sheets of material. As long as your material is able to be laser cut and is rigid enough, it can be used for thie mobile robot platforms.

### Laser Cutter Settings
Setting will vary widely between laser cutters, material, and material thickness. Perform some small test cuts to determine the optimal laser power and speed.

### Ensuring Correct Sizes
To ensure the DXF files are imported correctly into your laser cutting software, we provide some reference dimensions for the laser cut components:

- The diameter of the platforms is 354 mm (~14 inches)

### Component List
| File Name | Quantity per Robot | Preview |
|---|---|---|
| level1.DXF | 1 |  |
| level2.DXF | 1 |  |
| level3.DXF | 1 |  |
| level4.DXF | 1 |  |
| level5.DXF | 1 |  |
| level6.DXF | 1 |  |
| LIDAR_plate.DXF | 1 |  |
| control_panel.DXF | 1 |  |
| **Total** | 8 | |

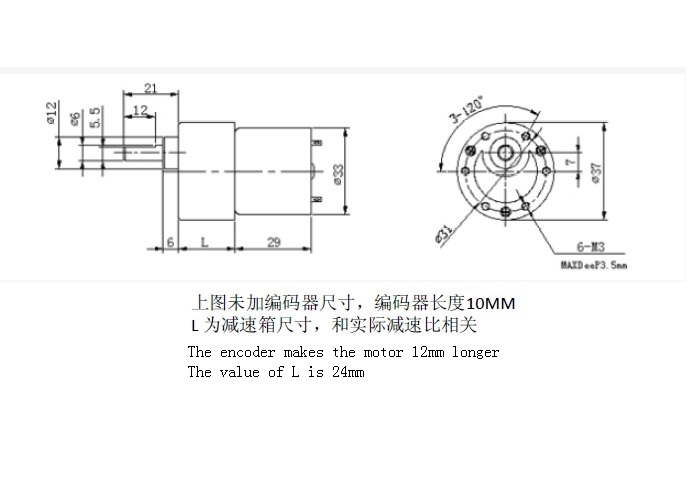
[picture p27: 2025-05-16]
CAD/MotorSpecs/FIT0403 - 122 rpm.jpg

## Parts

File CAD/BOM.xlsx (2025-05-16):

This page includes the components of the mobile robot
Note: The Quantity is listed per robot unless otherwise noted
Electronics
Item Name | Item Description | Item Link | Quantity | Other Notes
Nvidia Jetson Orin Nano | NVIDIA Jetson Orin Nano Super Developer Kit | https://www.amazon.com/dp/B0BZJTQ5YP?utm_source=nvidia&th=1 | 1
7.2 NiMh Battery | 7.2V 6200mAh NIMH Battery with Tamiya Connector | https://www.amazon.com/dp/B08P35DRNP/?coliid=IT2O6VDRELJUT&colid=PVITX9DKOJI6 | 2 | *May want multiple per robot so one can charge while using other battery pack
Tamiya to Lead Converter | Tamiya Style Plug Male to Wire Lead | https://www.amazon.com/dp/B08MFPJHWB/?coliid=I37PSX0JA3R3FS&colid=PVITX9DKOJI6 | 2
NiMh Battery Charger | 7.2V Ni-MH Battery Charger with Tamiya Connector | https://www.amazon.com/dp/B07ZNZC6KW/?coliid=I3VPMDBINFVX8Q&colid=PVITX9DKOJI6 | 2
Battery for Jetson | 12 V >=6000mAh, >=2.5A, DC Lithium Ion Battery with barrel jack output | https://www.amazon.com/dp/B00ME3ZH7C/?coliid=I3HMDU7MR6U9B&colid=PVITX9DKOJI6 | 1 | *May want multiple per robot so one can charge while using other battery pack
Battery for MCU | 5V >=2.4A, >=5000mAh Small Battery Pack with usb-a as output | https://www.amazon.com/dp/B083VRD7CX/?coliid=I3LSGKP9XGV86P&colid=PVITX9DKOJI6 | 1
DC Power Size Adapter | 5.5mm x 2.1mm Female to 5.5mm x 2.5mm Male Barrel Jack Adapter | https://www.amazon.com/dp/B07FJMX1YR/?coliid=I3FZIH2YKIM1T5&colid=PVITX9DKOJI6 | 1 | *Only necessary if Battery for Jetson DC Output size is 5.5mm x2.1 mm
Memory for Jetson | >= 1 TB NVME M.2 PCIe SSD Memory | https://www.amazon.com/dp/B07ZGJVTZK/?coliid=I2I1D18UDB0TJN&colid=PVITX9DKOJI6 | 1
Micro SD Card | >= 128 GB microSD UHS-I Memory Card | https://www.amazon.com/dp/B09X7BK27V/?coliid=I3JG5TEYVAKUUH&colid=PVITX9DKOJI6 | 1
WiFi Card | WiFi Card that Supports Roaming (M.2 Slot (Key-E, Type 2230)) | https://www.amazon.com/dp/B079QJQF4Y/?coliid=I2ZE4T1A5KEUOC&colid=PVITX9DKOJI6 | 1
DisplayPort Adapter | DisplayPort to HDMI Adapter | https://www.amazon.com/dp/B081GMCNNF/?coliid=I151P7LK9DALH9&colid=PVITX9DKOJI6 | 1
Multi USB port | USB-A Multi Port Splitter | https://www.amazon.com/dp/B07L32B9C2/?coliid=I2CL68SYM7HHD1&colid=PVITX9DKOJI6 | 1
Short (1ft) Micro-USB to USB | 1 ft Long USB-A to Micro USB 2.0 Cable | https://www.amazon.com/SUNGUY-3-Pack-Braided-Charging-Galaxy/dp/B07G934SJ9?sp_csd=d2lkZ2V0TmFtZT1zcF9hdGY | 1
Long (3ft) Micro-USB to USB | 3 ft Long USB-A to Micro USB 2.0 Cable | https://www.amazon.com/dp/B0D7C6YVZS/?coliid=I2B4FQC14U1WUB&colid=PVITX9DKOJI6 | 2
Long (3ft) HDMI Cable | 3 ft long HDMI Cable | https://www.amazon.com/Soonsoonic-Cables-HDCP2-2-Ethernet-Braided-Monitor/dp/B095WTCQYQ | 1 | *Only needed if Touch screen doesn't come with HDMI Cable
Sensors
Item Name | Item Description | Item Link | Quantity | Other Notes
RGB-D Camera | Orbbec Astra Pro Plus | https://store.orbbec.com/products/astra-pro-plus | 1
LiDAR Sensor | RPLiDAR A2M12 LiDAR Sensor | https://www.dfrobot.com/product-1461.html?gQT=1 | 1
USB Camera | Mini USB Camera for Facial Recognition | https://www.amazon.com/dp/B09BR1RNSN/?coliid=I192IBMJAURNTI&colid=3AQOJEVE8NOMZ | 1
Touch Screen/Monitor | Touch Screen Monitor for User Interaction | https://www.amazon.com/dp/B0BKGCB18T/?coliid=I7U5SC36TQYMS&colid=3OLRW5V2Y7BAF | 1
Mechanical
Item Name | Item Description | Item Link | Quantity | Other Notes
DC Motor with Encoder | 12 V DC Motors with Optical Encoder | https://www.dfrobot.com/product-1462.html | 2
Motor Shaft | D Axle 80x6mm Shafts | https://www.amazon.com/Accuracy-Industrial-Stainless-Machine-Equipment/dp/B08N5H4DGD | 2
Spider Coupler | 4mm to 6mm Flexible Coupler Shaft | https://www.amazon.com/Aopin-Flexible-Couplings-Coupler-Connector/dp/B08XJN9KMP | 2 | *May change if different motor is purchased
Bearings | Flanged Ball Bearing 6mmx15mmx5mm | https://www.amazon.com/uxcell-Bearing-6x15x5mm-Shielded-Bearings/dp/B07Z3F1MR5 | 4
Epoxy | Multi surface epoxy glue | https://www.amazon.com/Gorilla-Epoxy-Minute-ounce-Syringe/dp/B001Z3C3AG?mcid=702e3a04afff30e9b2abda067abf1045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 | 1 | *1 epoxy container is good for many robots
Wheels | 80 mm wheel --- Without Bearings! | https://www.amazon.com/NONMON-Inline-Wheels-Skates-Replacement/dp/B088RDVCT1 | 2 | *Can do bigger wheel as well
Screws | M3 Screws Assorted length with button head with nuts and washers | https://www.amazon.com/HELIFOUNER-Pieces-Button-Washers-Stainless/dp/B09GR7V65C?sp_csd=d2lkZ2V0TmFtZT1zcF9hdGY | 1 | *1 set is enough for several robots
Screws | M3 Screws 8 mm | https://www.amazon.com/Socket-Screws-Bolts-Thread-100pcs/dp/B07CMQ1SQH | 100 | *screws/robot
Screws | M6 Screw 12 mm | https://www.amazon.com/BNUOK-M6-1-0-Socket-Stainless-Spanner/dp/B0DHKZJNLQ | 1 | *For mounting Orbbec Astra camera
Heat Set Inserts | M3*4.6x5.7 mm Heat Set Inserts | https://www.amazon.com/Threaded-Inserts-Printing-Embedment-Automotive/dp/B0BQJ6CRNJ | 100
Ball Caster | Metal ball caster | https://www.dfrobot.com/product-225.html | 2
Other
Item Name | Item Description | Item Link | Quantity | Other Notes
Dupont connecting set | 2.54mm Dupont Connector Kit: male/female crimps, dupont housings | https://www.amazon.com/Taiss-Connector-Housing-Adaptor-Assortment/dp/B0B11SX39B | 1 | *1 set is enough for many robots
Wire Heat Shrink | Heat Shrink Tubing Kit (Only need a few per robot) | https://www.amazon.com/900Pcs-Shrink-Tubing-Industrial-Heat-Shrink/dp/B0B1D19LVW | 1 | *1 set is enough for many robots
Wire | 24 AWG Stranded Hook-Up Wire (Twisted pair nice, but not required) | https://www.amazon.com/Jameco-ValuePro-Stranded-Twisted-Hook-Up/dp/B0CQMSWVYY | 40 | *40 feet (12 m) total/robot (only 6 m needed if twisted pair)
Zip Ties | Zip Ties-8 inch | https://www.amazon.com/Hmrope-Premium-Plastic-Strength-Self-Locking/dp/B07TG9VMWY | 40 | *per robot (20 cm in length or similar)
Foam Bumpers | 1/2 inch Foam Pipe Insulation - 6 feet long | https://www.amazon.com/Insulation-Tubing-Guitar-Hollow-Protectors/dp/B0D21WRGLS | 5 | *per robot (or similar foam like material for bumpers, ~2 meters needed per level)
Thin Sheets of Wood for platforms | 1/8-1/4 inch (3-7mm) thick sheets of Duron wood (Tempered hardboard) | https://www.homedepot.com/p/Hardboard-Tempered-Panel-Common-1-8-in-4-ft-x-8-ft-Actual-0-115-in-x-47-7-in-x-95-7-in-832777/202189720 | 0.75 | *m^2 per robot, other materials can be used as long as stiff enough and can be laser cut
PLA Plastic | PLA Filament For 3D Printer |  | 550 | *grams filament per robot

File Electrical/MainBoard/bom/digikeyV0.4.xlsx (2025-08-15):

References | Value | Footprint | Mfr | Mfr P/N | Supplier 1 | Supplier 1 P/N | Quantity | Total Quantity | Adjusted Quantity
C1, C2, C3, C4, C5, C6, C7, C8, C9, C10, C19, C22, C23, C24, C27, C28, C30, C31, C32 | 0.1 uF | C_0805_2012Metric_Pad1.18x1.45mm_HandSolder | Samsung Electro-Mechanics | CL21B104KBCNNNC | DigiKey | 1276-1003-1-ND | 19 | 57 | 100
C11, C12, C13, C14 | 4.7 uF | C_0805_2012Metric_Pad1.18x1.45mm_HandSolder | Samsung Electro-Mechanics | CL21A475KAQNNNE | DigiKey | 1276-1244-1-ND | 4 | 12 | 15
C20, C26 | 0.47 uF | C_0805_2012Metric_Pad1.18x1.45mm_HandSolder | Samsung Electro-Mechanics | CL21B474KBFNNNE | DigiKey | 1276-1039-1-ND | 2 | 6 | 10
C21, C29 | 0.01 uF | C_0805_2012Metric_Pad1.18x1.45mm_HandSolder | KEMET | C0805C103K5RACTU | DigiKey | 399-C0805C103K5RACTUCT-ND | 2 | 6 | 10
C25, C33 | 100 uF | PCAP_8x10-ELECT_NCA-M | Nichicon | UWT1H101MNL1GS | DigiKey | 493-2226-1-ND | 2 | 6 | 0
C15 | 10 uF | CP_Radial_Tantal_D5.0mm_P2.50mm | KYOCERA AVX | TAP106K016CRW | DigiKey | 478-7366-1-ND | 1 | 3 | 0
R3, R4, R5, R6, R7, R8, R9, R10, R11, R15, R16 | 130R | R_0805_2012Metric_Pad1.20x1.40mm_HandSolder | Stackpole Electronics Inc | RMCF0805FT130R | DigiKey | RMCF0805FT130RCT-ND | 11 | 33 | 50
R20, R21, R22, R23, R24, R30, R31, R32, R33, R34 | 0R | R_0805_2012Metric_Pad1.20x1.40mm_HandSolder | Stackpole Electronics Inc | RMCF0805ZT0R00 | DigiKey | RMCF0805ZT0R00CT-ND | 10 | 30 | 50
R2, R12, R13, R14 | 1k | R_0805_2012Metric_Pad1.20x1.40mm_HandSolder | Stackpole Electronics Inc | RMCF0805FT1K00 | DigiKey | RMCF0805FT1K00CT-ND | 4 | 12 | 15
R26, R36, R47, R49 | 0.1R | R_0603_1608Metric_Pad0.98x0.95mm_HandSolder | Panasonic Electronic Components | ERJ-6DSJR10V | DigiKey | P19260CT-ND | 4 | 12 | 15
R1, R17, R27 | 10k | R_0805_2012Metric_Pad1.20x1.40mm_HandSolder | Stackpole Electronics Inc | RMCF0805FT10K0 | DigiKey | RMCF0805FT10K0CT-ND | 3 | 9 | 25
R18, R28 | 16k | R_0805_2012Metric_Pad1.20x1.40mm_HandSolder | Stackpole Electronics Inc | RMCF0805FT16K0 | DigiKey | 738-RMCF0805FT16K0CT-ND | 2 | 6 | 10
R19, R29 | 51k | R_0805_2012Metric_Pad1.20x1.40mm_HandSolder | Stackpole Electronics Inc | RMCF0805FT51K0 | DigiKey | RMCF0805FT51K0CT-ND | 2 | 6 | 10
R25, R35 | 1M | R_0805_2012Metric_Pad1.20x1.40mm_HandSolder | Stackpole Electronics Inc | RMCF0805FG1M00 | DigiKey | RMCF0805FG1M00CT-ND | 2 | 6 | 10
R48, R50 | 0.05 R | R_0603_1608Metric_Pad0.98x0.95mm_HandSolder | Panasonic Electronic Components | ERJ-L06KJ50MV | DigiKey | P50NLCT-ND | 2 | 6 | 10
D1, D2, D4, D6, D9, D10 | LED | LED_0805_2012Metric_Pad1.15x1.40mm_HandSolder | Harvatek Corporation | B1701URO-20D000114U1930 | DigiKey | 3147-B1701URO-20D000114U1930CT-ND | 6 | 18 | 22
D3, D5, D7 | LED | LED_0805_2012Metric_Pad1.15x1.40mm_HandSolder | Harvatek Corporation | B1701UD--20D000414U1930 | DigiKey | 3147-B1701UD--20D000414U1930CT-ND | 3 | 9 | 10
D11 | Status_LED | CONN3_22232031_MOL | Kingbright | WP59EGW/CA | DigiKey | 754-2191-ND | 1 | 3 | 3
U5, U6, U7, U8 | GSF7002DW | SOT-363_SC-70-6 | Good-Ark Semiconductor | GSF7002DW | DigiKey | 4786-GSF7002DWCT-ND | 4 | 12 | 0
U2, U3 | AP2114HA-3.3TRG1 | SOT-223_DIO-M | Diodes Incorporated | AP2114HA-3.3TRG1 | DigiKey | AP2114HA-3.3TRG1DICT-ND | 2 | 6 | 0
U10, U13 | DRV8842PWPR | PWP0028C_M | Texas Instruments | DRV8842PWPR | DigiKey | 296-29575-1-ND | 2 | 6 | 3
U1 | PIC32MZ2048EFH144-I/PL | LQFP144_PL_MCH-M | Microchip Technology | PIC32MZ2048EFH144-I/PL | DigiKey | PIC32MZ2048EFH144-I/PL-ND | 1 | 3 | 2
U9 | MCP2221A-I_SL | SOIC127P600X175-14N | Microchip Technology | MCP2221A-I/SL | DigiKey | MCP2221A-I/SL-ND | 1 | 3 | 2
F1 | 5A Fuse | FUSE_4628 | Keystone Electronics | 4628 | DigiKey | 36-4628-ND | 1 | 3 | 2
SW4, SW5, SW6 | User_Button | CONN_22232021_MOL | Molex | 22232021 | DigiKey | 900-0022232021-ND | 3 | 9 | 0
SW1 | Reset | SW_B3F-1000_OMR | Omron Electronics Inc-EMC Div | B3F-1020 | DigiKey | SW402-ND | 1 | 3 | 0
SW2 | 5V Bypass | SPDT_OS102011_CNK | C&K | OS102011MS2QN1 | DigiKey | CKN9565-ND | 1 | 3 | 3
SW3 | All Power Switch | 26-60-4040_MOL | E-Switch | RA83231100 | DigiKey | EG5682-ND | 1 | 3 | 3
J20, U11, U12 | Conn_01x06, Quad_Encoder_Motor | Molex_KK-254_AE-6410-06A_1x06_P2.54mm_Vertical | Molex | 22232061 | DigiKey | WM4204-ND | 3 | 9 | 9
J2, J3 | 3.3V Supply, 5V Supply | PinHeader_2x05_P2.54mm_Vertical | Adam Tech | PH2-10-UA | DigiKey | 2057-PH2-10-UA-ND | 2 | 6 | 6
J4, J9 | USB_B_Micro | AMPHENOL_10118193-0001LF | Amphenol ICC (FCI) | 10118193-0001LF | DigiKey | 609-4616-1-ND | 2 | 6 | 4
J5, J6 | Battery1 | CONN_1017514 | Phoenix Contact | 1017514 | DigiKey | 277-17504-ND | 2 | 6 | 3
J1 | SNAP Program | PinSocket_1x06_P2.54mm_Horizontal | Sullins Connector Solutions | PRPC006SBAN-M71RC | DigiKey | S1111EC-06-ND | 1 | 3 | 0
J18 | Conn_01x04 | Molex_PicoBlade_53047-0410_1x04_P1.25mm_Vertical | Molex | 530470410 | DigiKey | WM1733-ND | 1 | 3 | 4
J30 | Conn_01x08 | Molex_PicoBlade_53047-0810_1x08_P1.25mm_Vertical | Molex | 530470810 | DigiKey | WM1737-ND | 1 | 3 | 4
 |  | User Button | E-Switch | PS1024ALRED | DigiKey | EG2025-ND | 3 | 9 | 6
 |  | 2 Pin Female | Molex | 22013027 | DigiKey | 900-0022013027-ND | 3 | 9 | 0
 |  | 3 Pin Female | Molex | 22013037 | DigiKey | 900-0022013037-ND | 1 | 3 | 0
 |  | 6 Pin Female | Molex | 22012067 | DigiKey | WM2015-ND | 3 | 9 | 11
 |  | 3 Pin Male | Molex | 22232031 | DigiKey | WM4201-ND | 1 | 3 | 3
 |  | Big Crimps | Molex | 8650804 | DigiKey | WM2756CT-ND | 30 | 90 | 150
 |  | Picoblade Crimps | Molex | 500798000 | DigiKey | WM1142CT-ND | 12 | 36 | 100
 |  | 8 pin picoblade male | Molex | 510210800 | DigiKey | WM1726-ND | 1 | 3 | 8
 |  | 4 pin picoblade male | Molex | 510210400 | DigiKey | WM1722-ND | 1 | 3 | 11
 |  | Big 4 Pin Male | Molex | 26604040 | DigiKey | WM4622-ND | 1 | 3 | 2
 |  | Big 4 Pin Female | Molex | 9508041 | DigiKey | WM2124-ND | 1 | 3 | 2
 |  | Big Crimps | Molex | 8500008 | DigiKey | WM20948CT-ND | 5 | 15 | 10
 |  | 5A Fuse | Littlefuse Inc. | 0217005.MXP | DigiKey | F1725-ND | 1 | 3 | 0
IMU-C1, C2 |  | 100 nF | Samsung Electro-Mechanics | CL21B104KBCNNNC | DigiKey | 1276-1003-1-ND | 2 | 6 | 0
IMU-U1 |  | BMI323 | Bosch | BMI323 | Digikey | 828-BMI323CT-ND | 1 | 3 | 4
IMU-J3 |  | Conn_01x08_Pin | Molex | 530480810 | DigiKey | WM1748-ND | 1 | 3 | 4
IMU-J3-1 |  | Conn_01x08_RCPT | Molex | 510210800 | DigiKey | WM1726-ND | 1 | 3 | 0
IMU-J3-2 |  | Conn_Crimp | Molex | 500798000 | DigiKey | WM1142CT-ND | 8 | 24 | 0
C1, C2, C3, C4, C5, C6 |  | 0.1 uF | Samsung Electro-Mechanics | CL21B104KBCNNNC | DigiKey | 1276-1003-1-ND | 6 | 6 | 0
R4, R5 |  | 130R | Stackpole Electronics Inc | RMCF0805FT130R | DigiKey | RMCF0805FT130RCT-ND | 2 | 2 | 0
R1 |  | 10k | Stackpole Electronics Inc | RMCF0805JT10K0 | DigiKey | RMCF0805JT10K0CT-ND | 1 | 1 | 0
R2 |  | 1k | Stackpole Electronics Inc | RMCF0805FT1K00 | DigiKey | RMCF0805FT1K00CT-ND | 1 | 1 | 0
R3 |  | 100k | Stackpole Electronics Inc | RMCF0805FG100K | DigiKey | RMCF0805FG100KCT-ND | 1 | 1 | 0
D1, D2 |  | LED | Harvatek Corporation | B1701URO-20D000114U1930 | DigiKey | 3147-B1701URO-20D000114U1930CT-ND | 2 | 2 | 0
U1 |  | GSF7002DW | Good-Ark Semiconductor | GSF7002DW | DigiKey | 4786-GSF7002DWCT-ND | 1 | 1 | 0
SW1 |  | B3F-1020 | Omron Electronics Inc-EMC Div | B3F-1020 | DigiKey | SW402-ND | 1 | 1 | 0
IC1 |  | PIC32MK0128MCA048-I_Y8X | Microchip Technology | PIC32MK0128MCA048T-I/Y8X | DigiKey | 150-PIC32MK0128MCA048T-I/Y8XCT-ND | 1 | 1 | 0
J2, J3, J5 |  | Conn_01x06 | Molex | 22232061 | DigiKey | WM4204-ND | 3 | 3 | 0
J1 |  | Conn_01x05_Pin | Amphenol ICC (FCI) | 10129379-910002BLF | DigiKey | 10129379-910002BLF-ND | 1 | 1 | 0
J6 |  | Conn2MCU-Female | Molex | 22012067 | DigiKey | WM2015-ND | 3 | 3 | 0
J7 |  | Conn2MCU-Crimp | Molex | 8510108 | DigiKey | WM19393CT-ND | 18 | 18 | 0
C2, C3 |  | 1uF | Samsung Electro-Mechanics | 1276-1066-1-ND | DigiKey | 1276-1066-1-ND | 2 | 12 | 15
C1 |  | 0.1uF | Samsung Electro-Mechanics | CL21B104KBCNNNC | DigiKey | 1276-1003-1-ND | 1 | 6 | 0
R2, R3 |  | 10k | Stackpole Electronics Inc | RMCF0805FT10K0 | DigiKey | RMCF0805FT10K0CT-ND | 2 | 12 | 0
R1 |  | 4.7R | YAGEO | RC0805FR-074R7L | DigiKey | 311-4.70CRCT-ND | 1 | 6 | 10
U1 |  | SGP41-D-R4 | Sensirion AG | SGP41-D-R4 | DigiKey | 1649-SGP41-D-R4CT-ND | 1 | 6 | 7
U2 |  | SHT40-AD1B-R3 | SHT40-AD1B-R3 | SHT40-AD1B-R3 | DigiKey | 1649-SHT40-AD1B-R3CT-ND | 1 | 6 | 7
J1 |  | Conn_01x04_Pin | Molex | 530480410 | DigiKey | WM1744-ND | 1 | 6 | 7
J1-1 |  | Conn_01x04_RCPT | Molex | 510210400 | DigiKey | WM1722-ND | 1 | 6 | 0
J1-2 |  | Conn_Crimp | Molex | 500798000 | DigiKey | WM1142CT-ND | 4 | 24 | 0
C1 | 0.1 uF | C_0805_2012Metric_Pad1.18x1.45mm_HandSolder | Samsung Electro-Mechanics | CL21B104KBCNNNC | DigiKey | 1276-1003-1-ND | 1 | 2 | 0
MK1 | ICS-43434 | MIC_ICS-43434 | TDK InvenSense | ICS-43434 | DigiKey | 1428-1066-1-ND | 1 | 2 | 0
J1 | Conn2MCU | CONN_22-05-3061_MOL | Molex | 22053061 | DigiKey | WM4304-ND | 1 | 2 | 0
 | Female |  |  |  |  |  | 1 | 2 | 0
 | Crimps |  |  |  |  |  | 1 | 2 | 0

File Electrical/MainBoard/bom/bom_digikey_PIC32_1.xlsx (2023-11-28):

References | Value | Footprint | Mfr | Mfr P/N | Supplier 1 | Supplier 1 P/N | Quantity
C1, C2, C3, C4, C5, C6, C7, C8, C9, C10, C17, C19, C22, C23, C24, C27, C28, C30, C31, C32, C35, C36 | 0.1 uF | C_0805_2012Metric_Pad1.18x1.45mm_HandSolder | Samsung Electro-Mechanics | CL21B104KBCNNNC | DigiKey | 1276-1003-1-ND | 22
C11, C12, C13, C14 | 4.7 uF | C_0805_2012Metric_Pad1.18x1.45mm_HandSolder | Samsung Electro-Mechanics | CL21A475KAQNNNE | DigiKey | 1276-1244-1-ND | 4
C16, C21, C29 | 0.01 uF | C_0805_2012Metric_Pad1.18x1.45mm_HandSolder | Samsung Electro-Mechanics | CL21B103KBANNNC | DigiKey | 1276-1015-1-ND | 3
C20, C26 | 0.47 uF | C_0805_2012Metric_Pad1.18x1.45mm_HandSolder | Samsung Electro-Mechanics | CL21B474KBFNNNE | DigiKey | 1276-1039-1-ND | 2
C25, C33 | 100 uF | PCAP_8x10-ELECT_NCA-M | Nichicon | UWT1H101MNL1GS | DigiKey | 493-2226-1-ND | 2
C15 | 10 uF | CP_Radial_Tantal_D5.0mm_P2.50mm | KYOCERA AVX | TAP106K016CRW | DigiKey | 478-7366-1-ND | 1
C18 | 2.2 uF | C_0805_2012Metric_Pad1.18x1.45mm_HandSolder | Samsung Electro-Mechanics | CL21B225KPFNNNE | DigiKey | 1276-1188-1-ND | 1
R3, R4, R5, R6, R7, R8, R9, R10, R11, R15, R16 | 130R | R_0805_2012Metric_Pad1.20x1.40mm_HandSolder | Stackpole Electronics Inc | RMCF0805FT130R | DigiKey | RMCF0805FT130RCT-ND | 11
R20, R21, R22, R23, R24, R30, R31, R32, R33, R34 | 0R | R_0805_2012Metric_Pad1.20x1.40mm_HandSolder | Stackpole Electronics Inc | RMCF0805ZT0R00 | DigiKey | RMCF0805ZT0R00CT-ND | 10
R2, R12, R13, R14, R37, R38, R39, R40 | 1k | R_0805_2012Metric_Pad1.20x1.40mm_HandSolder | Stackpole Electronics Inc | RMCF0805FT1K00 | DigiKey | RMCF0805FT1K00CT-ND | 8
R1, R17, R27 | 10k | R_0805_2012Metric_Pad1.20x1.40mm_HandSolder | Stackpole Electronics Inc | RMCF0805FT10K0 | DigiKey | RMCF0805FT10K0CT-ND | 3
R18, R28 | 16k | R_0805_2012Metric_Pad1.20x1.40mm_HandSolder | Stackpole Electronics Inc | RMCF0805FT16K0 | DigiKey | 738-RMCF0805FT16K0CT-ND | 2
R19, R29 | 51k | R_0805_2012Metric_Pad1.20x1.40mm_HandSolder | Stackpole Electronics Inc | RMCF0805FT51K0 | DigiKey | RMCF0805FT51K0CT-ND | 2
R25, R35 | 1M | R_0805_2012Metric_Pad1.20x1.40mm_HandSolder | Stackpole Electronics Inc | RMCF0805FG1M00 | DigiKey | RMCF0805FG1M00CT-ND | 2
R26, R36 | 0.25R | R_0805_2012Metric_Pad1.20x1.40mm_HandSolder | Stackpole Electronics Inc | CSR0805FKR250 | DigiKey | CSR0805FKR250CT-ND | 2
D1, D2, D4, D6, D9, D10 | LED | LED_0805_2012Metric_Pad1.15x1.40mm_HandSolder | Würth Elektronik | 150080RS75000 | DigiKey | 732-4984-1-ND | 6
D3, D5, D7 | LED | LED_0805_2012Metric_Pad1.15x1.40mm_HandSolder | Würth Elektronik | 150080VS75000 | DigiKey | 732-4986-1-ND | 3
D8 | Status_LED | CONN3_22232031_MOL | Kingbright | WP115WGYW | DigiKey | 754-1864-ND | 1
U5, U6, U7, U8 | GSF7002DW | SOT-363_SC-70-6 | Good-Ark Semiconductor | GSF7002DW | DigiKey | 4786-GSF7002DWCT-ND | 4
U2, U3 | AP2114HA-3.3TRG1 | SOT-223_DIO-M | Diodes Incorporated | AP2114HA-3.3TRG1 | DigiKey | AP2114HA-3.3TRG1DICT-ND | 2
U10, U13 | DRV8842PWPR | PWP0028C_M | Texas Instruments | DRV8842PWPR | DigiKey | 296-29575-1-ND | 2
U11, U12 | Quad_Encoder | CONN_22-23-2041_MOL | Molex | 22232041 | DigiKey | WM4202-ND | 2
U1 | PIC32MZ2048EFH144-I/PL | LQFP144_PL_MCH-M | Microchip Technology | PIC32MZ2048EFH144-I/PL | DigiKey | PIC32MZ2048EFH144-I/PL-ND | 1
U4 | ICM-42688-P | LGA14_2P5X3X0P91_TDK-M | TDK InvenSense | ICM-42688-P | DigiKey | 1428-ICM-42688-PCT-ND | 1
U9 | MCP2221A-I_SL | SOIC127P600X175-14N | Microchip Technology | MCP2221A-I/SL | DigiKey | MCP2221A-I/SL-ND | 1
U15 | M95M01-DFMN6TP | SO8N_4X5X1P27_STM-M | STMicroelectronics | M95512-WMN6TP | DigiKey | 497-8697-1-ND | 1
F1 | 5A Fuse | FUSE_4628 | Keystone Electronics | 4628 | DigiKey | 36-4628-ND | 1
SW7, SW8, SW9, SW10 | SW_SPST | CONN_22232021_MOL | Molex | 22232021 | DigiKey | 900-0022232021-ND | 4
SW4, SW5, SW6 | User_Button | CONN_22232021_MOL | Molex | 22232021 | DigiKey | 900-0022232021-ND | 3
SW1 | Reset | SW_B3F-1000_OMR | Omron Electronics Inc-EMC Div | B3F-1020 | DigiKey | SW402-ND | 1
SW2 | 5V Bypass | SPDT_OS102011_CNK | C&K | OS102011MS2QN1 | DigiKey | CKN9565-ND | 1
SW3 | All Power Switch | 26-60-4040_MOL | E-Switch | RA83231100 | DigiKey | EG5682-ND | 1
M1, M2 | Motor_DC | CONN_1890963_PXC | Phoenix Contact | 1890963 | DigiKey | 277-5953-ND | 2
J16, J19, J20, J21, J23 | Conn_02x03_Odd_Even | PinHeader_2x03_P2.54mm_Vertical | Amphenol ICC (FCI) | 10129381-906002BLF | DigiKey | 10129381-906002BLF-ND | 5
J13, J14, J15 | Refl_PCB_Connect | CONN3_22232031_MOL | Molex | 22232031 | DigiKey | WM4201-ND | 3
J4, J9 | USB_B_Micro | AMPHENOL_10118193-0001LF | Amphenol ICC (FCI) | 10118193-0001LF | DigiKey | 609-4616-1-ND | 2
J5, J6 | Battery1 | CONN_1017514 | Phoenix Contact | 1017514 | DigiKey | 277-17504-ND | 2
J18, J22 | Conn_02x02_Odd_Even | PinHeader_2x02_P2.54mm_Vertical | Amphenol ICC (FCI) | 10129381-904003BLF | DigiKey | 10129381-904003BLF-ND | 2
J1 | SNAP Program | PinSocket_1x06_P2.54mm_Horizontal | Sullins Connector Solutions | PRPC006SBAN-M71RC | DigiKey | S1111EC-06-ND | 1
J2 | 3.3V Supply | PinHeader_2x05_P2.54mm_Vertical | Adam Tech | PH2-10-UA | DigiKey | 2057-PH2-10-UA-ND | 1
J3 | 5V Supply | PinHeader_2x05_P2.54mm_Vertical | Adam Tech | PH2-10-UA | DigiKey | 2057-PH2-10-UA-ND | 1
J7 | GPIO1 | PinHeader_2x05_P2.54mm_Vertical | Amphenol ICC (FCI) | 10129381-910001BLF | DigiKey | 10129381-910001BLF-ND | 1
J8 | Conn_02x04_Odd_Even | PinHeader_2x04_P2.54mm_Vertical | Amphenol ICC (FCI) | 10129381-908001BLF | DigiKey | 10129381-908001BLF-ND | 1
J17 | MEM2061-01-188-00-A | MEM2061-01-188-00-A_GCT | GCT | MEM2061-01-188-00-A | DigiKey | 2073-MEM2061-01-188-00-ACT-ND | 1
J24 | Conn_01x04 | CONN_22-23-2041_MOL | Molex | 22232041 | DigiKey | WM4202-ND | 1

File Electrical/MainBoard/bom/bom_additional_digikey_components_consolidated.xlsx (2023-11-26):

Description | Mfr | Mfr P/N | Supplier | Supplier P/N | Quantity
5A Fuse | Littlefuse Inc. | 0617005.MXP | DigiKey | F11916-ND | 1
User Button | E-Switch | PS1024ALRED | DigiKey | EG2025-ND | 3
Limit Switch | TE Connectivity ALCOSWITCH Switches | SAJ101XBL0N74SNOPTQ | DigiKey | 450-SAJ101XBL0N74SNOPTQ-ND | 4
2 Pin Female | Molex | 22013027 | DigiKey | 900-0022013027-ND | 10
3 Pin Female | Molex | 22013037 | DigiKey | 900-0022013037-ND | 1
4 Pin Female | Molex | 22013047 | DigiKey | WM2002-ND | 2
Crimps | Molex | 8650804 | DigiKey | WM2756CT-ND | 34
Big 4 Pin Male | Molex | 26604040 | DigiKey | WM4622-ND | 1
Big 4 Pin Female | Molex | 9508041 | DigiKey | WM2124-ND | 1
Big Crimps | Molex | 8500008 | DigiKey | WM20948CT-ND | 4

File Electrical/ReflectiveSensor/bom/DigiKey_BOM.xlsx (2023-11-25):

References | Value | Footprint | Description | Mfr | Mfr P/N | Supplier 1 | Supplier 1 P/N | Quantity
C1 | 0.1 uF | C_0805_2012Metric_Pad1.18x1.45mm_HandSolder | CAP CER 0.1UF 50V X7R 0805 | Samsung Electro-Mechanics | CL21B104KBCNNNC | DigiKey | 1276-1003-1-ND | 1
R1 | 100R | R_0805_2012Metric_Pad1.20x1.40mm_HandSolder | RES 100 OHM 1% 1/8W 0805 | Stackpole Electronics Inc | RMCF0805FT100R | DigiKey | RMCF0805FT100RCT-ND | 1
R2 | 10k | R_0805_2012Metric_Pad1.20x1.40mm_HandSolder | RES 10K OHM 1% 1/8W 0805 | Stackpole Electronics Inc | RMCF0805FT10K0 | DigiKey | RMCF0805FT10K0CT-ND | 1
K1 | QRE1113GR | ARUSM-313_100CY_FAS-M | SENSOR OPTO TRANS REFL SMD PHOTO | onsemi | QRE1113GR | DigiKey | QRE1113GRCT-ND | 1

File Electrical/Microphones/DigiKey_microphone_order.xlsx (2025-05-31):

References | Value | Mfr | Mfr P/N | Supplier 1 | Supplier 1 P/N | Quantity
C1 | 0.1 uF | Samsung Electro-Mechanics | CL21B104KBCNNNC | DigiKey | 1276-1003-1-ND | 1
MK1 | ICS-43434 | TDK InvenSense | ICS-43434 | DigiKey | 1428-1066-1-ND | 1
J1 | Conn2MCU | Molex | 22053061 | DigiKey | WM4304-ND | 1
J2 | Conn2MCU-Female | Molex | 22012067 | DigiKey | WM2015-ND | 1
J3 | Conn2MCU-Crimp | Molex | 8510108 | DigiKey | WM19393CT-ND | 6

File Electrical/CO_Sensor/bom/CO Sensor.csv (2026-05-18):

 | Sourced | Placed | References | Value | Footprint | Supplier 1 | Supplier 1 P/N | Quantity
1 |  |  | C1, C2, C4 | 0.1uF | C_0805_2012Metric_Pad1.18x1.45mm_HandSolder | DigiKey | 1276-1003-1-ND | 3
2 |  |  | C3 | 10uF | C_0805_2012Metric_Pad1.18x1.45mm_HandSolder | DigiKey | 1276-1096-1-ND | 1
3 |  |  | R1, R2, R3 | 1M 0.1% | R_0805_2012Metric_Pad1.20x1.40mm_HandSolder | DigiKey | P1MDACT-ND | 3
4 |  |  | R4 | 47k 0.1% | R_0805_2012Metric_Pad1.20x1.40mm_HandSolder | DigiKey | P47KDACT-ND | 1
5 |  |  | R5 | 1k 1% | R_0805_2012Metric_Pad1.20x1.40mm_HandSolder | DigiKey | RMCF0805FT1K00CT-ND | 1
6 |  |  | U1 | ENS130 | ENS130 | DigiKey | 2618-ENS130-ND | 1
7 |  |  | U2 | TP5552-VR | VS1MSOP-8-A_TPK-M | DigiKey | 5503-TP5552-VRCT-ND | 1
8 |  |  | U3 | SMMBFJ175LT1G | SOT-23_ONS-M | DigiKey | 488-SMMBFJ175LT1GCT-ND | 1
9 |  |  | J1 | Conn_01x03_Pin | PinHeader_1x03_P2.54mm_Vertical |  |  | 1

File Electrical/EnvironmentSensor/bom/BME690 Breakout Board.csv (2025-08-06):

References | Value | Mfr | Mfr P/N | Supplier 1 | Supplier 1 P/N | Quantity
C1, C2 | 0.1uF | Samsung Electro-Mechanics | CL21B104KBCNNNC | DigiKey | 1276-1003-1-ND | 2
IC1 | BME690 | Bosch | BME690 | DigiKey | 828-BME690CT-ND | 1
J1 | Conn_01x06_Pin | Molex | 530480610 | DigiKey | WM1746-ND | 1
J1-1 | Conn_01x06_Rcpt | Molex | 510210600 | DigiKey | WM1724-ND | 1
J1-2 | Conn_Crimp | Molex | 500798000 | DigiKey | WM1142CT-ND | 6

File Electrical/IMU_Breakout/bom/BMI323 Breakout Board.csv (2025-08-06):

References | Value | Mfr | Mfr P/N | Supplier 1 | Supplier 1 P/N | Quantity
C1, C2 | 100 nF | Samsung Electro-Mechanics | CL21B104KBCNNNC | DigiKey | 1276-1003-1-ND | 2
U1 | BMI323 | Bosch | BMI323 | Digikey | 828-BMI323CT-ND | 1
J3 | Conn_01x08_Pin | Molex | 530480810 | DigiKey | WM1748-ND | 1
J3-1 | Conn_01x08_RCPT | Molex | 510210800 | DigiKey | WM1726-ND | 1
J3-2 | Conn_Crimp | Molex | 500798000 | DigiKey | WM1142CT-ND | 8

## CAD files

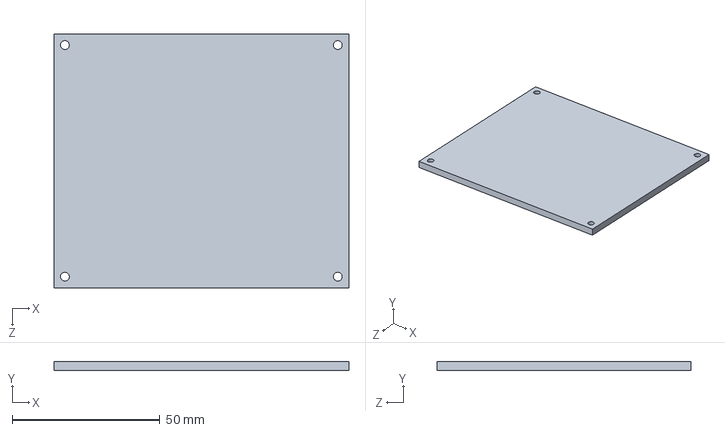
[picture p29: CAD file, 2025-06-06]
CAD/Inventor/solidworks/E - Electronics/Main Board.SLDPRT
100.0 x 3.17 x 86.0 mm

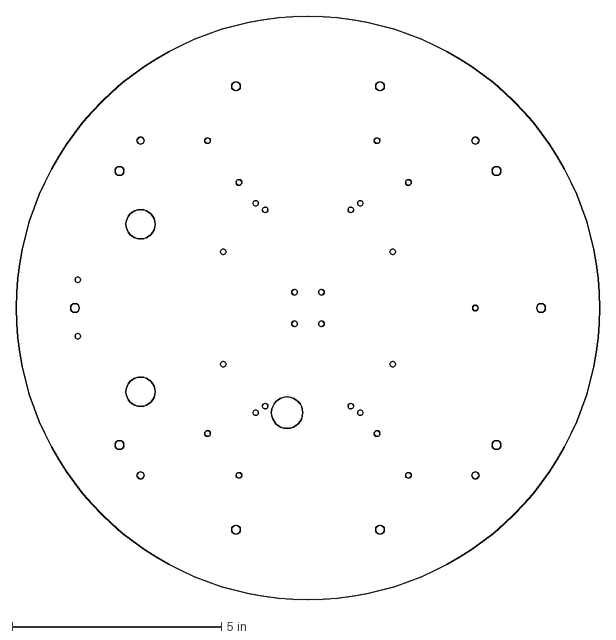
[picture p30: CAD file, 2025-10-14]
CAD/dxf/level2_short.dxf
13.9 x 13.9 in

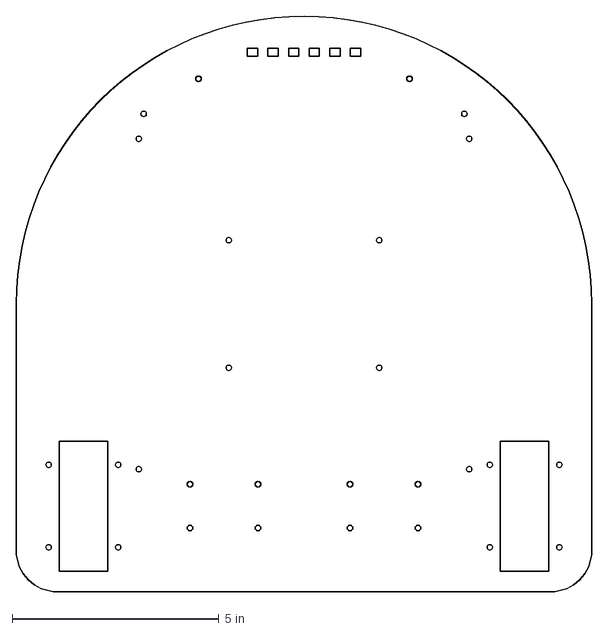
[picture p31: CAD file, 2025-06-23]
CAD/Inventor/C - Chassis/dxf/layer1_car.dxf
13.9 x 13.9 in

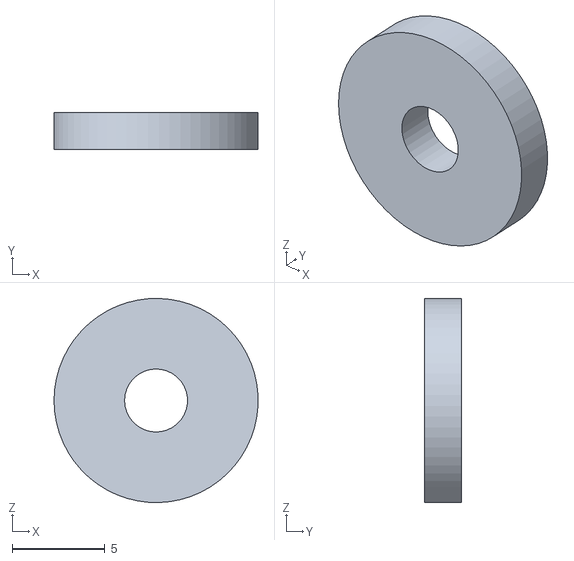
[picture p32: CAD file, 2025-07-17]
CAD/Inventor/C - Chassis/stl/caster_2mm_spacer.stl
11.0 x 2.00 x 11.0

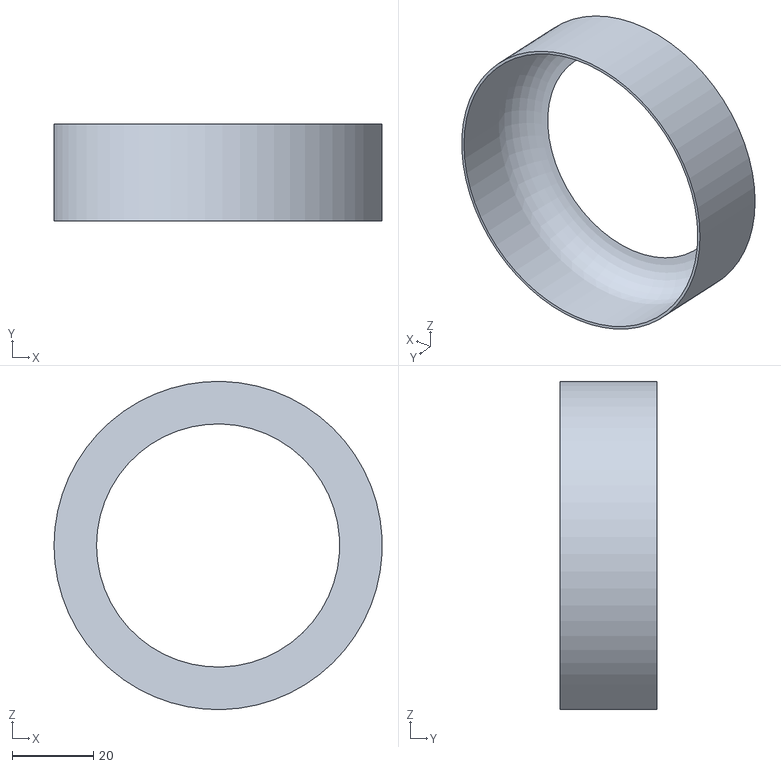
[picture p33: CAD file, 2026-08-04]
CAD/Inventor/D - DriveTrain/stl/pla_wheel_shell_81_od_1.5_thickness.stl
80.9 x 24.0 x 81.0

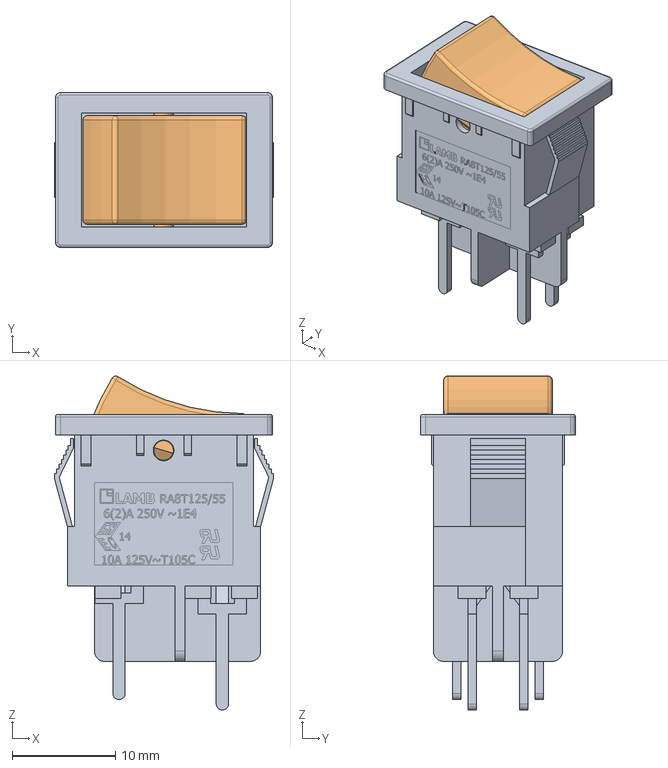
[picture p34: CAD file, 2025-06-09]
CAD/Inventor/E - Electronics/rocker_switch.stp
21.2 x 15.0 x 32.3 mm

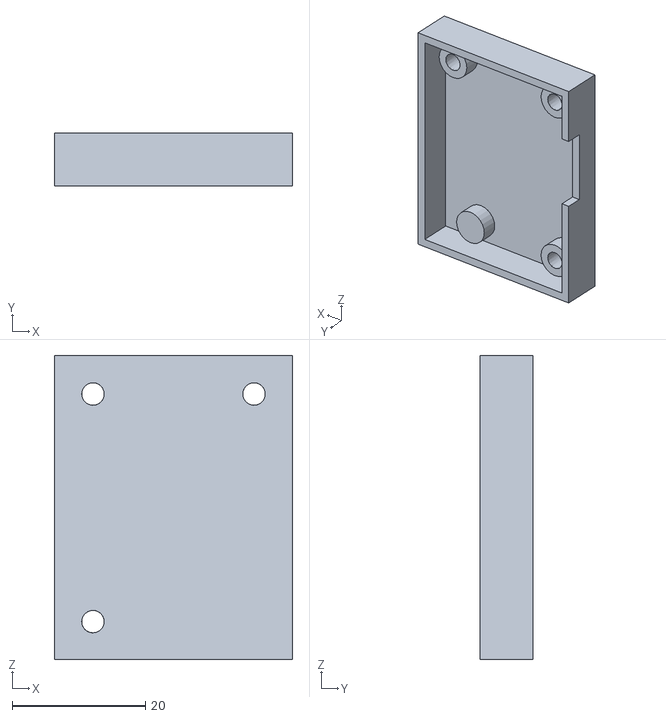
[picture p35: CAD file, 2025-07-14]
CAD/Inventor/E - Electronics/stl/microphone_MCU_case.stl
35.8 x 7.96 x 45.7

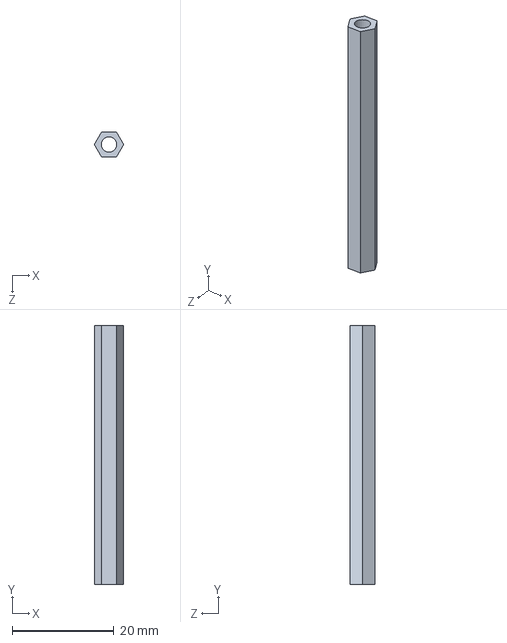
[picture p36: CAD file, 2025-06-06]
CAD/Inventor/solidworks/C - Chassis/2_inch_hex_standoff.SLDPRT
5.77 x 50.8 x 5.00 mm

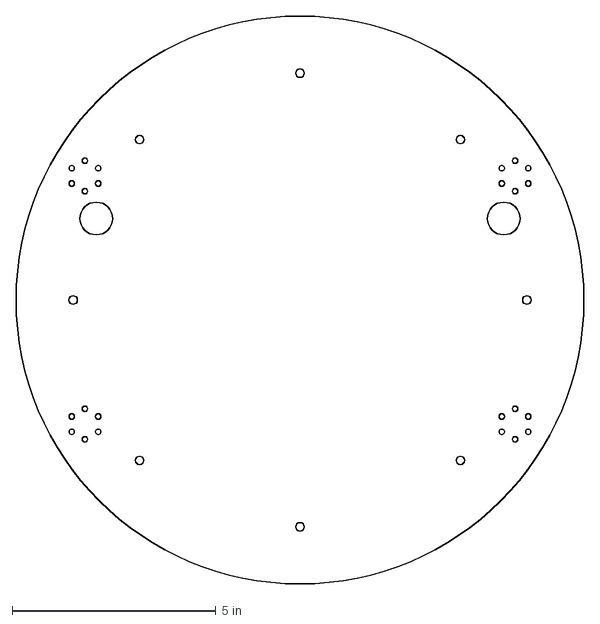
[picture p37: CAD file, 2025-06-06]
CAD/Inventor/solidworks/C - Chassis/tall/dxf/level4_5_tall.DXF
13.9 x 13.9 in

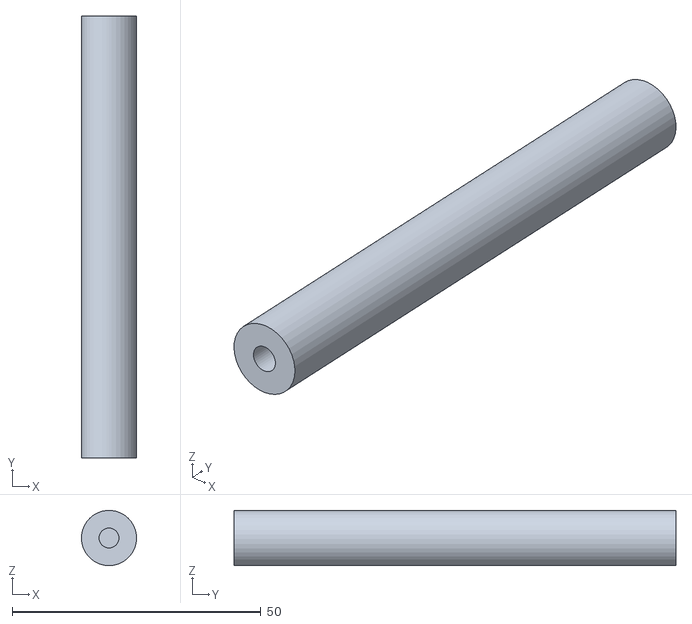
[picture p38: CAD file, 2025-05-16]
CAD/Inventor/solidworks/C - Chassis/tall/stls/3.5_inch_cir_standoff.STL
11.1 x 88.9 x 11.1

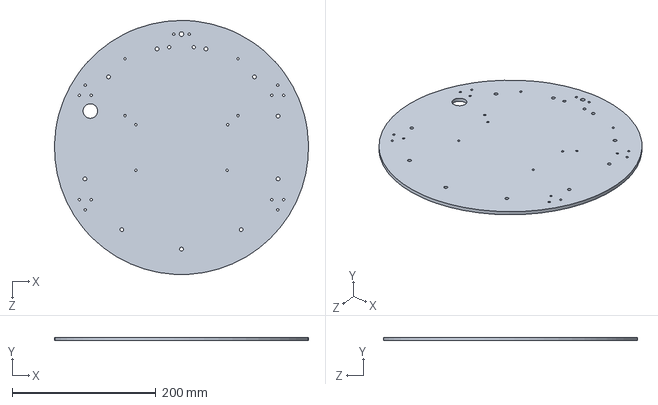
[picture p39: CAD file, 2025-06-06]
CAD/Inventor/solidworks/C - Chassis/tall/top_level.SLDPRT
353.8 x 4.76 x 354.0 mm

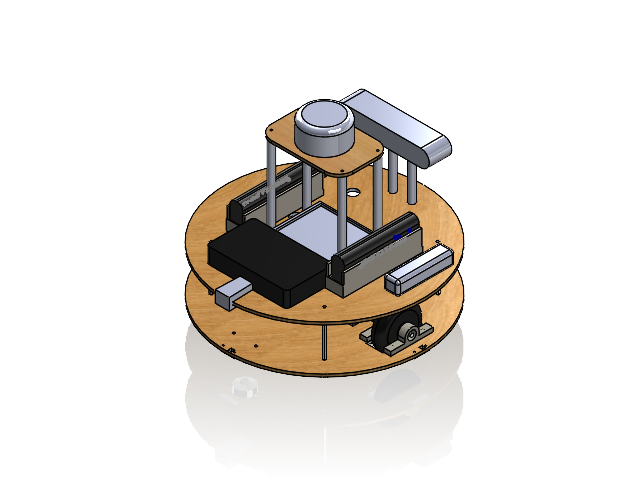
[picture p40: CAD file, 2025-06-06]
CAD/Inventor/solidworks/robot_assembly - 120rpm.SLDASM
wheel_bearing x 4
wheel x 2
Main Board
3_inch_hex_standoff x 4
layer_2_base_top
ball_caster x 2
drive_shaft x 2
ball_bearing x 4
Button.step x 3
reflective_sensor x 3
control_panel
LED
NiMH_battery x 2
wheel_mount x 4
camera
6_inch_cir_standoff x 4
LIDAR_plate
A2_LIDAR
NiMH_holder x 2
Lion_5V
IMU breakout
12V_Battery
motor_holder_FIT0403_122rpm x 2
motor_FIT0403_122rpm x 2
layer_1_floor-rpm130
shaft_coupler 6 mm x 2
motor strap_FIT0403_122rpm
jetson_orin_nano_platform
battery_clip
wheel_spacer_0.2 x 4

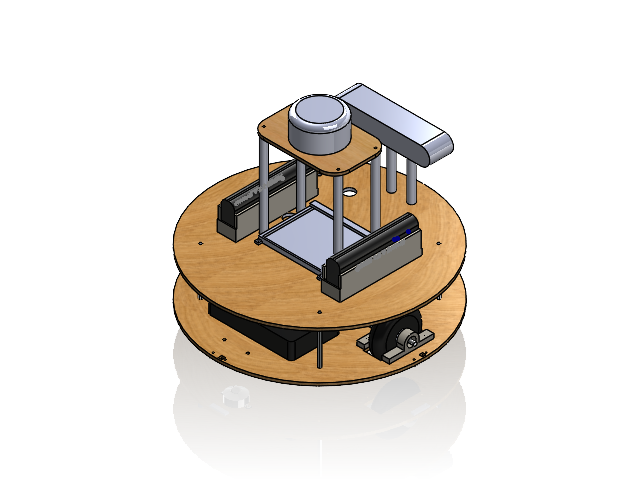
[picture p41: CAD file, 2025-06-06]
CAD/Inventor/solidworks/robot_assembly.SLDASM
layer_1_floor
wheel_bearing x 4
wheel x 2
Main Board
3_inch_hex_standoff x 4
layer_2_base_top
ball_caster x 2
drive_shaft x 2
ball_bearing x 4
motor x 2
shaft_coupler x 2
Button.step x 3
reflective_sensor x 3
control_panel
LED
NiMH_battery x 2
motor_holder x 2
wheel_mount x 4
motor strap x 2
jetson_orin_nano_holder
camera
6_inch_cir_standoff x 4
LIDAR_plate
A2_LIDAR
NiMH_holder x 2
Lion_5V
IMU breakout
12V_Battery

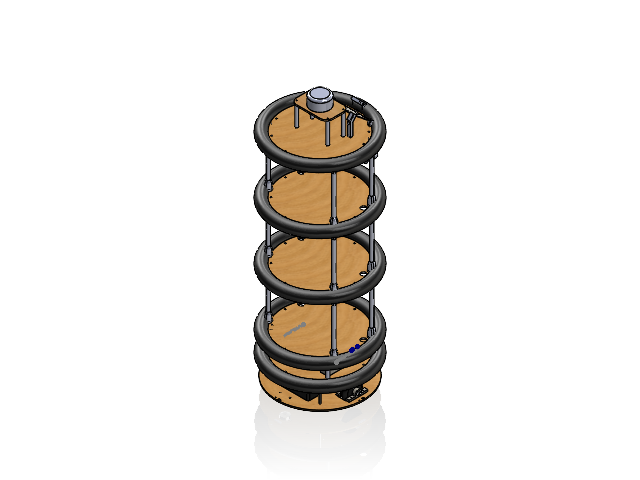
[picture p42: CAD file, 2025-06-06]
CAD/Inventor/solidworks/robot_assembly - tall.SLDASM
layer_1_floor
wheel_bearing x 4
wheel x 2
Main Board
3_inch_hex_standoff x 4
ball_caster x 2
drive_shaft x 2
ball_bearing x 4
motor x 2
shaft_coupler x 2
Button.step x 3
reflective_sensor x 3
control_panel
LED
NiMH_battery x 2
motor_holder x 2
wheel_mount x 4
motor strap x 2
jetson_orin_nano_holder
NiMH_holder x 2
Lion_5V
IMU breakout
12V_Battery
upper_level x 2
level2_tall
level3_tall
top_level
10_inch_spacers_3prong x 12
3_in_stand_offs x 4
A2_LIDAR
camera
monitor
top_support_right
bottom_support_left
bottom_support_right
top_support_left
LIDAR_plate
3_inch_cir_standoff x 4
Arducam_holder
Arducam
Arducam_pin x 2
foam x 5

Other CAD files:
CAD/Inventor/solidworks/Display/Arducam_assembly.SLDASM
CAD/Inventor/solidworks/Display/Assem1.SLDASM
CAD/Inventor/C - Chassis/drawings/layer1.dwg
CAD/Inventor/D - DriveTrain/drawings/motor_holder.dwg
CAD/Inventor/C - Chassis/3.5inch_standoff.ipt
CAD/Inventor/C - Chassis/3inch_standoff.ipt
CAD/Inventor/C - Chassis/6inch_standoff.ipt
CAD/Inventor/C - Chassis/8inch_spacer.ipt
CAD/Inventor/C - Chassis/9inch_spacer.ipt
CAD/Inventor/C - Chassis/LiDAR_plate.ipt
CAD/Inventor/C - Chassis/OldVersions/3.5inch_standoff.0002.ipt
CAD/Inventor/C - Chassis/OldVersions/3inch_standoff.0008.ipt
CAD/Inventor/C - Chassis/OldVersions/6inch_standoff.0009.ipt
CAD/Inventor/C - Chassis/OldVersions/8inch_spacer.0001.ipt
CAD/Inventor/C - Chassis/OldVersions/9inch_spacer.0001.ipt
CAD/Inventor/C - Chassis/OldVersions/LiDAR_plate.0003.ipt
CAD/Inventor/C - Chassis/OldVersions/ball_caster.0001.ipt
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

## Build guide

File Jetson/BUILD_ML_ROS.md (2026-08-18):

# Build `ml_ros` from scratch (optional)

Most setups should pull the pre-built image from GHCR instead. See [Docker Setup](README.md#docker-setup) in the Jetson README.

These steps worked for an NVIDIA Jetson Orin Nano when assembling the image locally before it was published to GHCR. Complete Docker system setup in the [Jetson README](README.md#docker-setup) first (jetson-containers, data root, restart Docker).

1) Choose a base container. I like l4t-ml since it contains cuda enabled pytorch, cuda enabled tensorflow2, and cuda enabled opencv. The full list of containers can be found https://github.com/dusty-nv/jetson-containers/tree/master

    Now, run the container, e.g.:
    ```
	jetson-containers run $(autotag l4t-ml)
    ```

2) Now we can install ROS. For example, for ROS Noetic, follow the instructions here: https://wiki.ros.org/noetic/Installation/Ubuntu

    **IMPORTANT**: Install the **ROS-Base** version. The other version will attempt to modify the opencv, which we cannot do! Thus, install the bare bones version and the selectively install additional packages we may need.

    The following is also useful to put in your `~/.bashrc` file
    ```
    source /workspace/catkin_ws/devel/setup.bash
    export ROS_IP=192.168.xx.xx
    export ROS_MASTER_URI=http://$ROS_IP:11311
    export ROBOT_ID=x
    ```

3) Install any additional ros packages you need, e.g.
    ```
	sudo apt install ros-noetic-PACKAGE
    ```
    I installed the following:
    - tf2-msgs
    - tf
    - gmapping
    - diagnostic-updater
    
    For the camera to work, I find it necessary to first run:
    ```
    apt-get purge -y '*opencv*'
    ```
    Then, follow instructions at https://github.com/satomm1/ros_astra_camera, with the following exception: run these lines outside of the docker container
    ```
    ./scripts/create_udev_rules
    sudo udevadm control --reload && sudo  udevadm trigger
    ```
 
4) Install other python packages you need.

    **IMPORTANT**: Any package which has an opencv-python dependency must be sure not to modify the opencv-python package already installed from the original container. Updating will break the package!

    Some packages I install include:
    - spidev
    - confluent-kafka
    - rospy-message-converter
    - pyignite
    - matplotlib
    - scipy
    - ultralytics****be careful with opencv-python here!

5) Install Cyclone DDS and it’s python binding.

    Follow the directions of https://github.com/eclipse-cyclonedds/cyclonedds to first install cycloneDDS. Be careful! Check what the latest version of the cyclonedds python binding is and match this version!  The install directory should be /path/to/cyclonedds/install. Next:
    ```
    export CYCLONEDDS_HOME="$(pwd)/install"
    ```
    Even better, put this in the `~/.bashrc` file since we need this anytime we use the python binding. Last, we install the python binding via:
    ```
    pip3 install cyclonedds --no-binary cyclonedds
    ```

6) Commit the docker container so you can use it later, e.g.:
	docker commit c3f279d17e0a ml_ros:latest

7) Now, to run the container, we can use the command:
    ```
	jetson-containers run $(autotag ml_ros:latest)
    ```

    You can include any of the usual docker commands with this. For example, my full command is:
    ```
    jetson-containers run -v ~/workspaces/catkin_ws:/workspace/catkin_ws -v ~/gemini_api:/gemini_code -v /dev/bus/usb:/dev/bus/usb -v /dev/video0:/dev/video0 -v /dev/video1:/dev/video1 -i --device=/dev/ttyUSB0 --device=/dev/spidev0.0 --rm --privileged --name ros_noetic $(autotag ml_ros:latest)
    ```
    OR
    ```
    sudo docker run --runtime nvidia --network=host -v ~/workspaces/catkin_ws:/workspace/catkin_ws -v ~/gemini_api:/gemini_code -v /dev/bus/usb:/dev/bus/usb -v /dev/video0:/dev/video0 -v /dev/video1:/dev/video1 -it --device=/dev/ttyUSB0 --device=/dev/spidev0.0 --rm --privileged --name ros_noetic ml_ros:latest
    ```

8) To save the image (for easy loading on a new machine), use the following command:
    ```
	docker save myimage:latest | gzip > myimage_latest.tar.gz
    ```

If everything has gone according to plan, you should now have a docker container which has ROS, cuda enabled pytorch/tensorflow, and everything else you might need!

Return to [Setting Up ROS Workspace](README.md#setting-up-ros-workspace) in the Jetson README.

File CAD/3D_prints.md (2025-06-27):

# Components to be 3D printed

Please visit the `stl` directory to obtain these files. For full construction instructions, visit the [Mechanical README](./README.md).

> [!NOTE] 
> Some of these STL files may need to be modified depending on the materials you purchase. For example, the motor holders and wheel bearing blocks will change depending on the thickness of the hardwood.

> [!NOTE] 
> If your ball bearings have flanges, 3D print the `wheel_bearing_block.STL` file. If they don't have flanges, print the `wheel_bearing_block_no_flange.STL` file.

Here at Stanford, a Prusa MK3.9 3D printer (Lab64) or Bambu Lab P1S (PRL AMPS) 3D printer is used. For reference, the estimated filament and time to print all of the components are provided on these 3D printers using the following printer settings:
- Filament: PLA
- Nozzle Size: 0.4 mm diameter
- Infill: 15%
- Layer Height: 0.15 mm (Prusa), 0.2 mm (Bambu)
- Supports: “everywhere”
- Brim: enabled 
- Speed: default machine settings (Prusa infill is 200 mm/s, Bambu infill is 270 mm/s)

## 3D Printed Parts List
The table below contains all the parts to be 3D printed. Components designated with a \* are components that do not depend on the specific materials purchased (i.e., doesn't depend on the motor, wheel size, wood thickness).

### Heat Set Inserts
Some of the components are designed to be used with M3 heat set inserts. Heat set inserts are small brass inserts that are melted into the plastic using a soldering iron (I recommend a low temperature of ~400F/200C). They provide strong, threaded connection points for screws (and are used instead of nuts). These parts are desiged for M3 heat set inserts with diameter 4.6 mm and length 5.7 mm.

> [!TIP]
> IF you are not familiar with installing heat set inserts, watch this quick video: https://youtu.be/P7nHyI1TwKY?t=189.

### Ensuring Correct Sizes
To ensure the STL files are imported correctly into your 3D printing software, we provide some reference dimensions for the 3D printed components:

- The length of the bearing blocks should be 3 inches (76 mm)
- The lengths of the 3 inch, 3.5 inch, and 9 inch standoffs should be the length designated in the file name

### Component List
| File Name | Quantity per Robot | Time per Robot (Prusa MK3.9/Bambu Lab P1S) | Filament per Robot (g, estimated) | Preview |
|---|---|--- | ---|---|
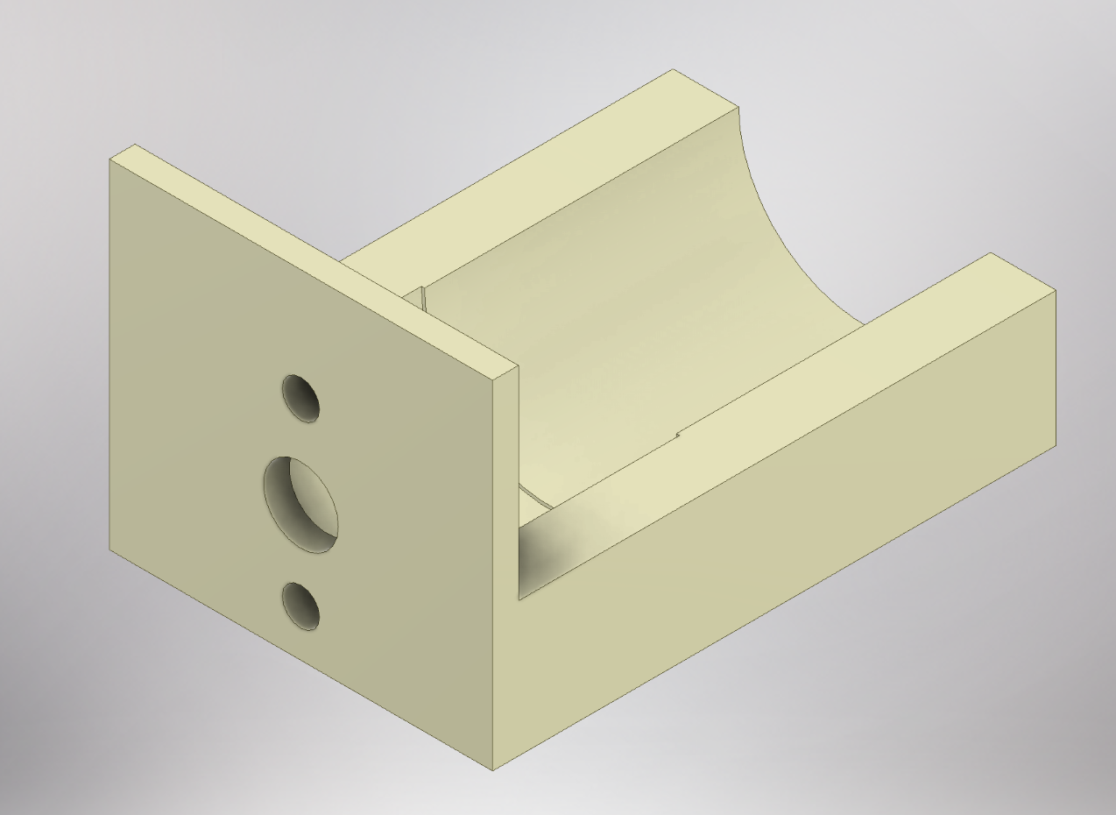
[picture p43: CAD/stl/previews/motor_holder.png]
| motor_holder.STL | 2 | 1 hr 17 min/45 min | 21.56 |  |
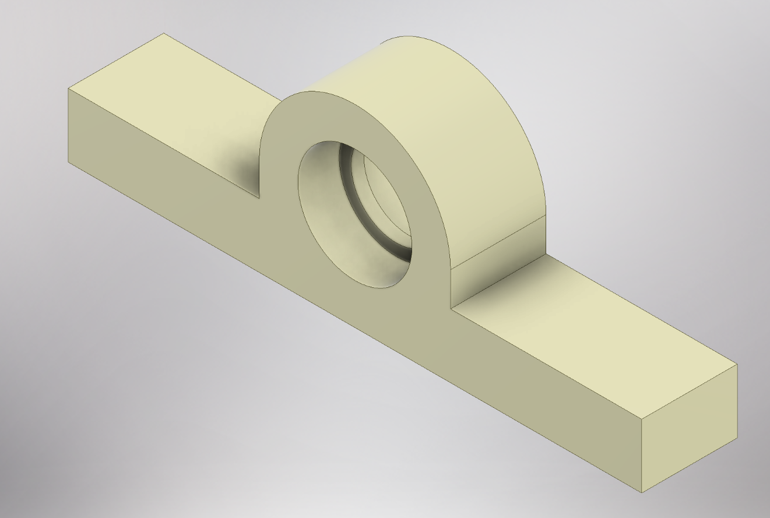
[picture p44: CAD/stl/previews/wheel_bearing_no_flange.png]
| wheel_bearing_block.STL OR wheel_bearing_block_no_flange.STL | 4 | 1 hr 23 min/50 min | 24.6 |  |
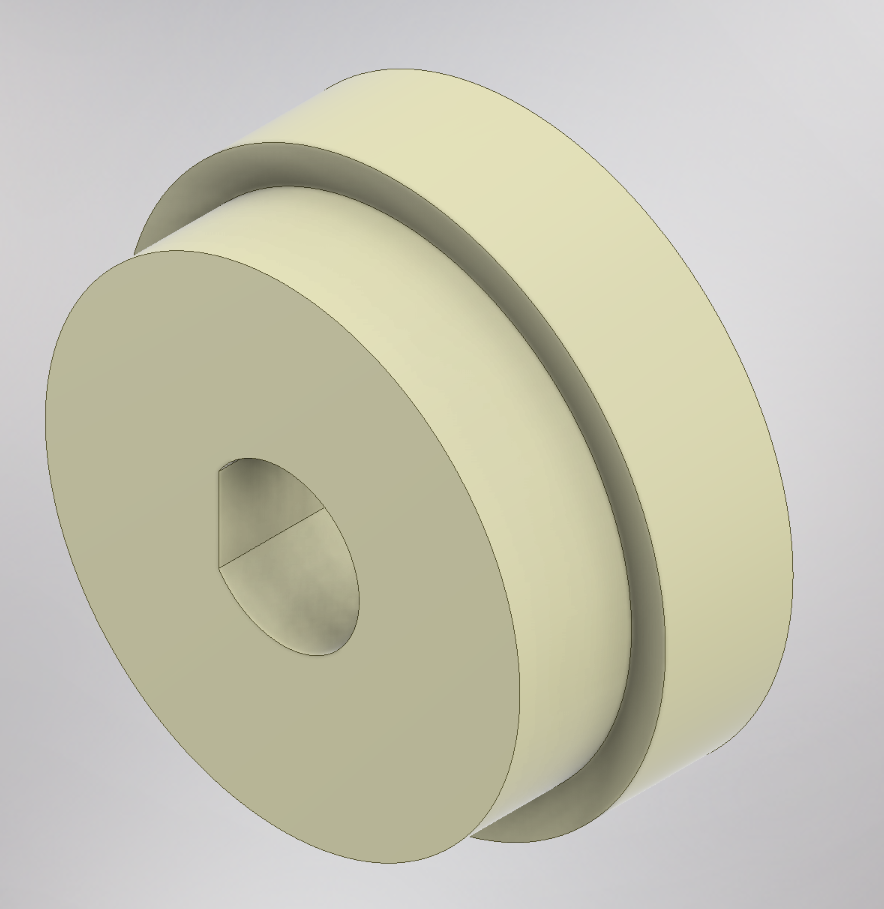
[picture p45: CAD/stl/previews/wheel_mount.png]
| * wheel_mount.STL | 4 | 27 min/23 min | 7.8 |  |
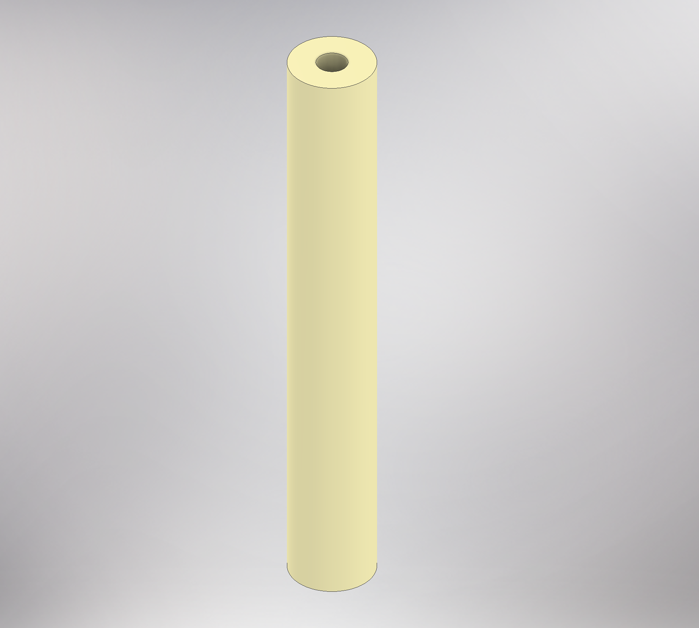
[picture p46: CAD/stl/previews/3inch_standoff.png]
| * 3_in_stand_offs.STL | 8 | 1 hr 45 min/1 hr 18 min | 35.2 |  |
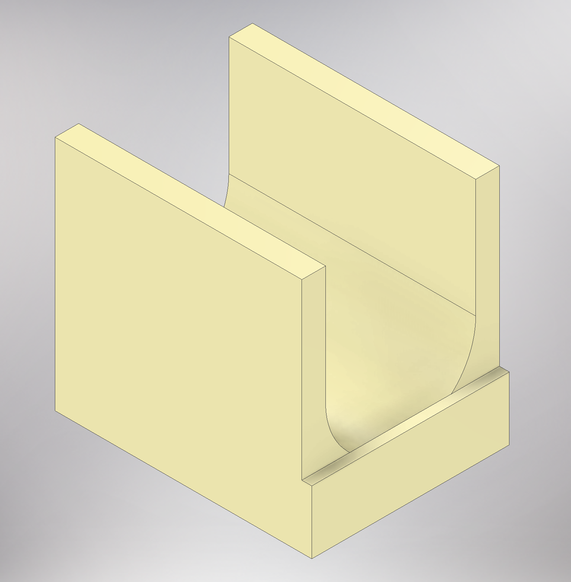
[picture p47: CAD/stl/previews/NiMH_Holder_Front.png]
| * NiMH_Holder_Front.STL | 2 | 1 hr 8 min/45 min | 24.02 |  |
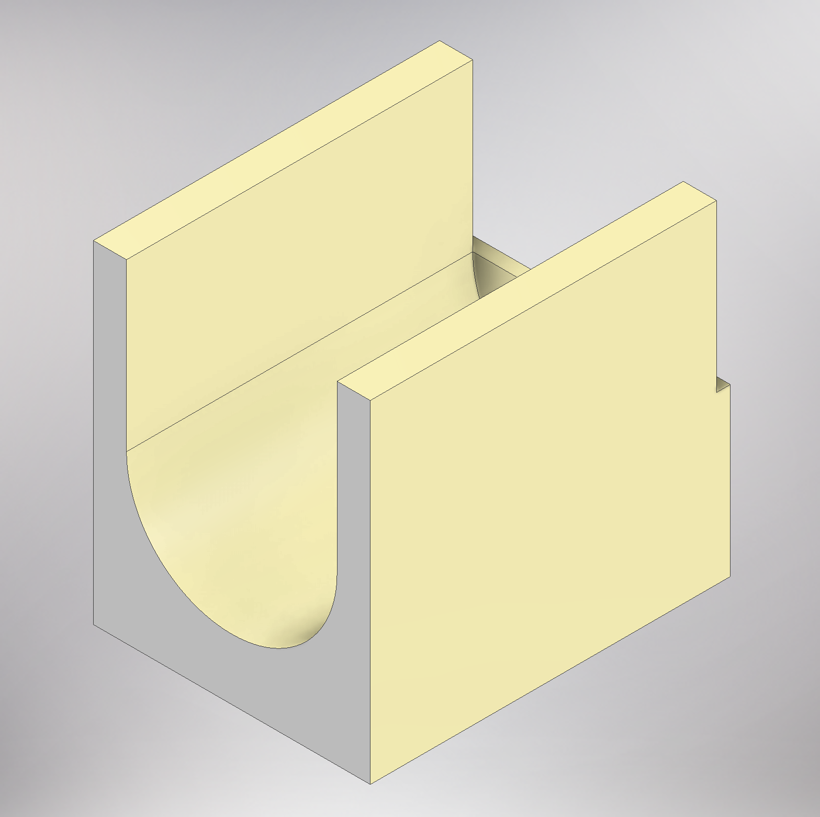
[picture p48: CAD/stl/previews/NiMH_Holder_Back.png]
| * NiMH_Holder_Back.STL | 2 | 1 hr 9 min/45 min | 24.78 |  |
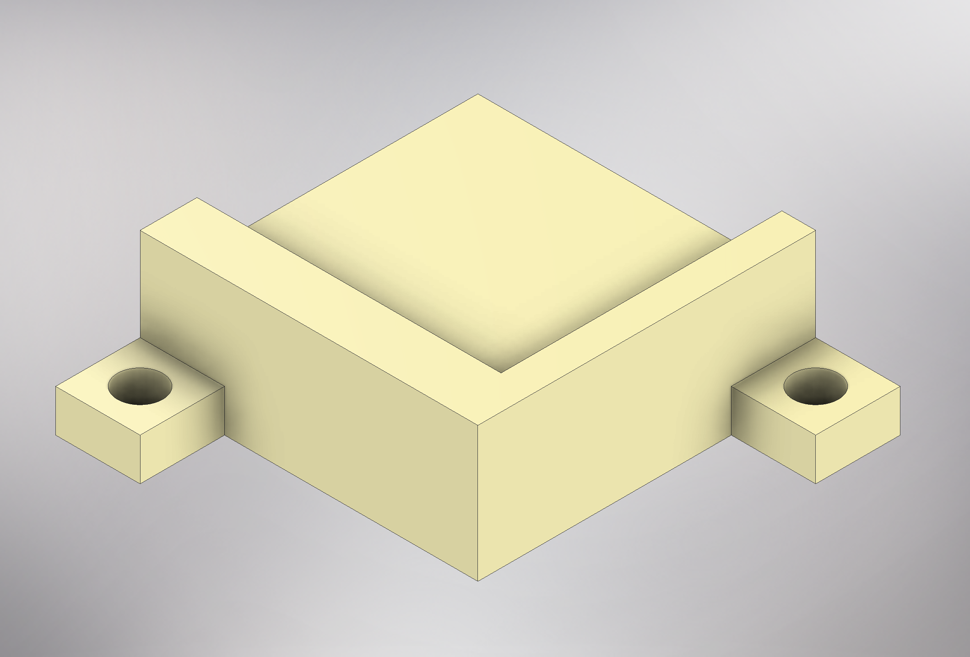
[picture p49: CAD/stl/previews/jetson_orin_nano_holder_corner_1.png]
| * jetson_orin_nano_holder_corner_1 | 2 | 20 min/17 min | 6.5 |  |
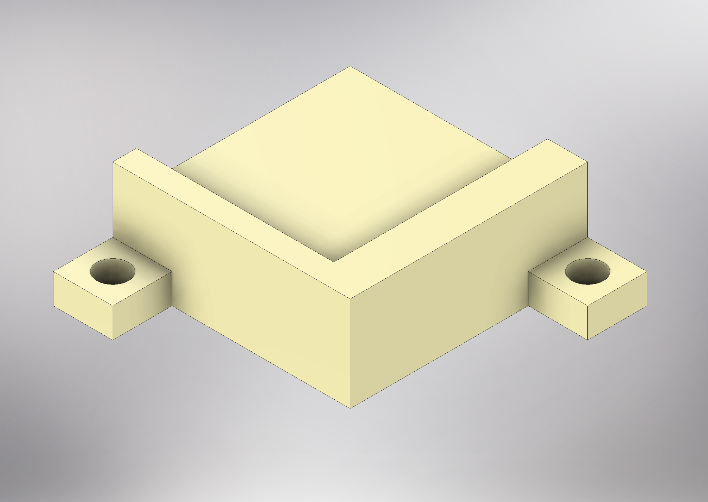
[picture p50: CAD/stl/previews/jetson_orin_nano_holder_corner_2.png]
| * jetson_orin_nano_holder_corner_2 | 2 | 20 min/17 min | 6.5 |  |
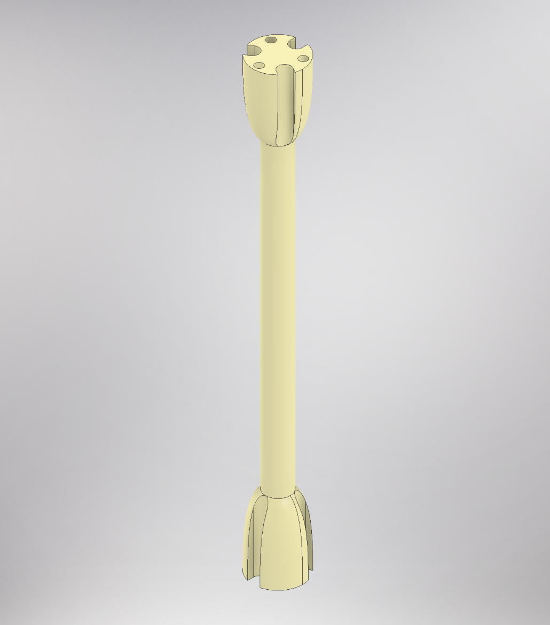
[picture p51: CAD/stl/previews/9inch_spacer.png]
| * 9_inch_spacer.STL | 12 | 18 hr/15 hr | 351.36 |  |
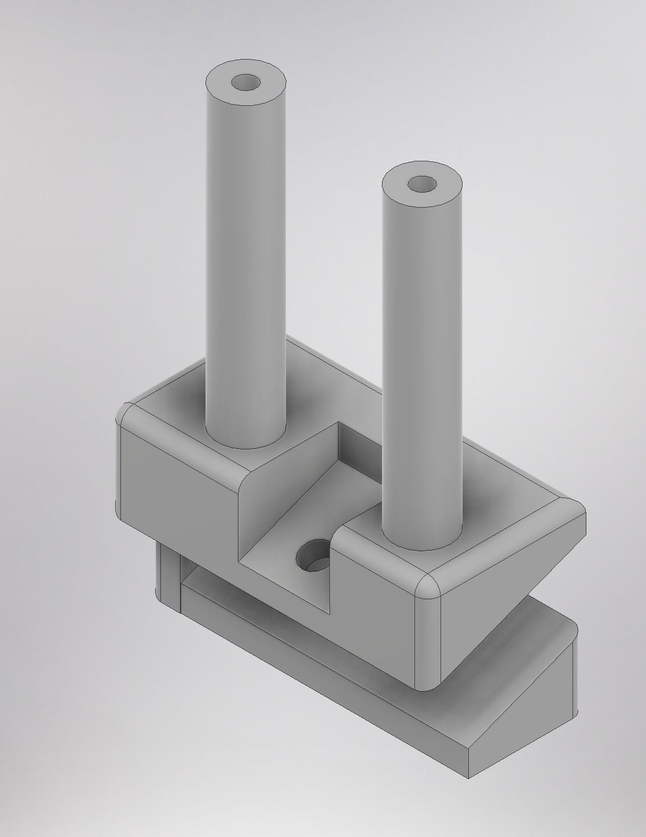
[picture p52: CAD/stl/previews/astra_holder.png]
| astra_holder.STL | 1 | 1 hr 15 min/53 min | 25.12 |  |
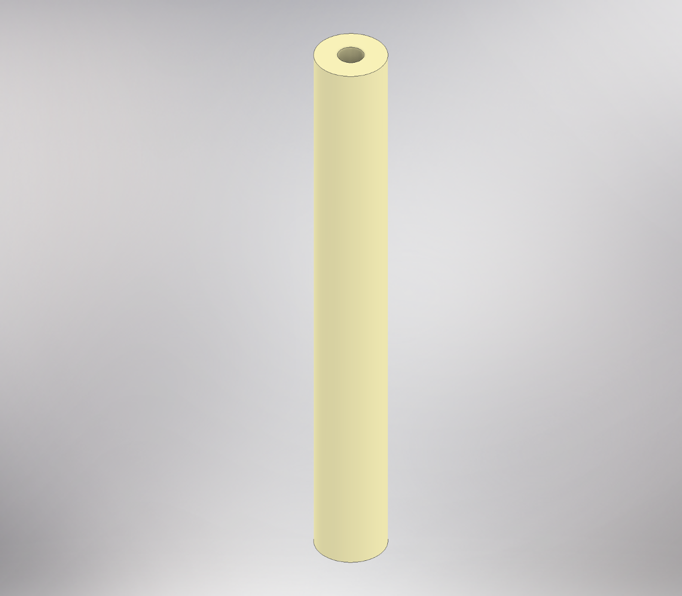
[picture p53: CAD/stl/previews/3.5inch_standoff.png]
| * 3.5_inch_standoff.STL | 4 | 52 min/45 min | 19.84 |  |
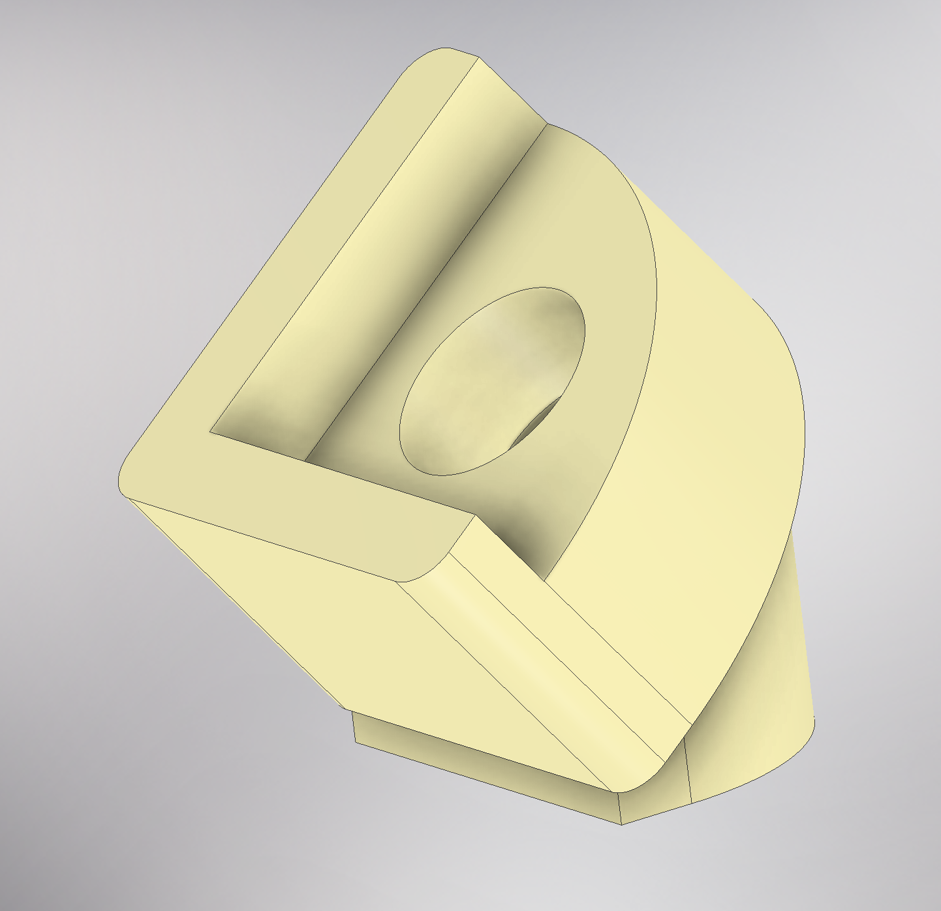
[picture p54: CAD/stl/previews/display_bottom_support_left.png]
| display_bottom_support_left.STL | 1 | 15 min/6 min | 1.7 |  |
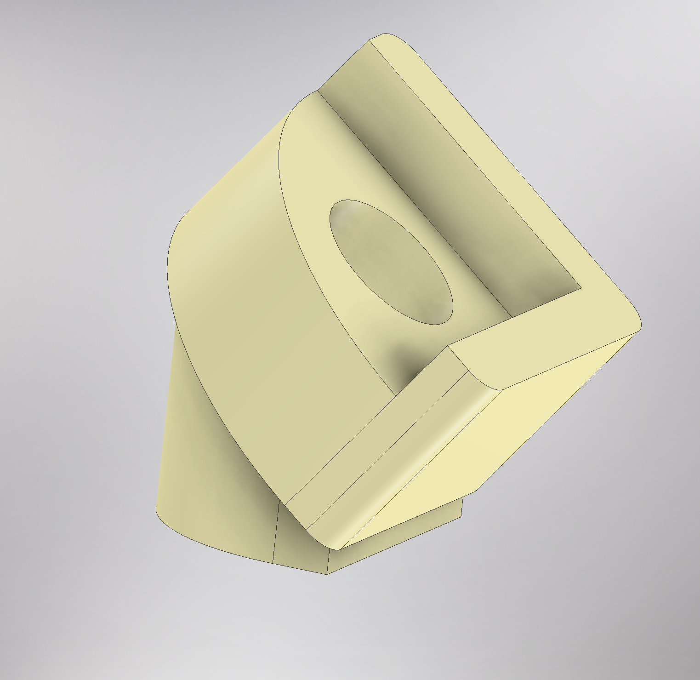
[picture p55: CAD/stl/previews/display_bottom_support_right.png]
| display_bottom_support_right.STL | 1 | 15 min/6min | 1.7 |  |
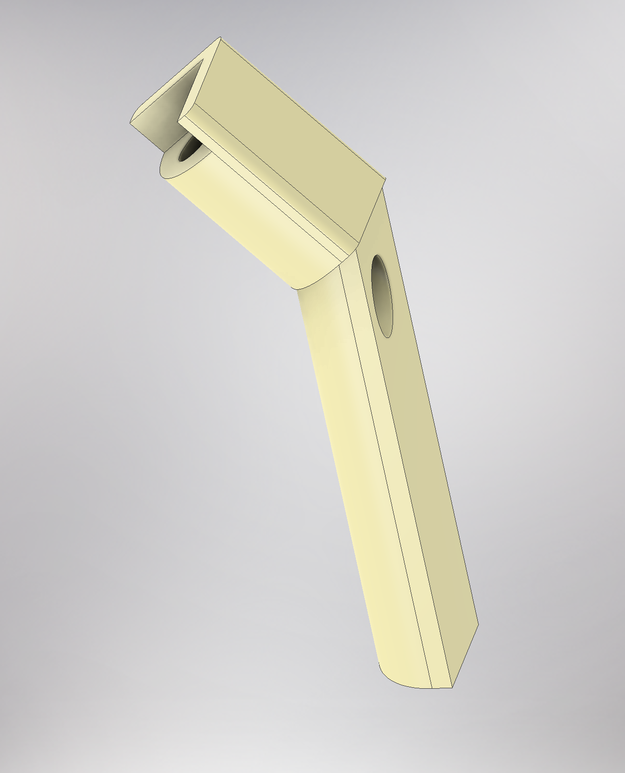
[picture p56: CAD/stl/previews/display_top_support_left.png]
| display_top_support_left.STL | 1 | 23 min/18 min | 6.27 |  |
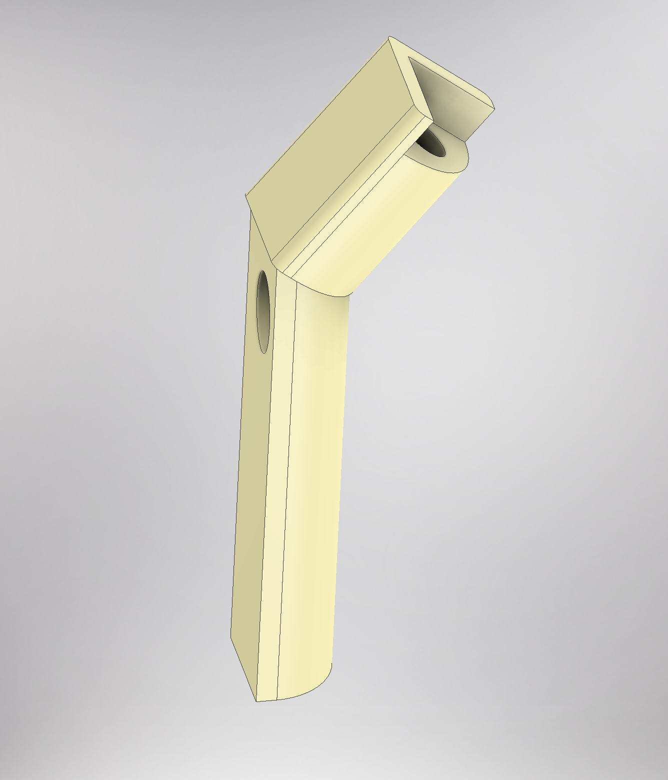
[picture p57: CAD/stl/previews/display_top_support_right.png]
| display_top_support_right.STL | 1 | 23 min/18 min | 6.27 |  |
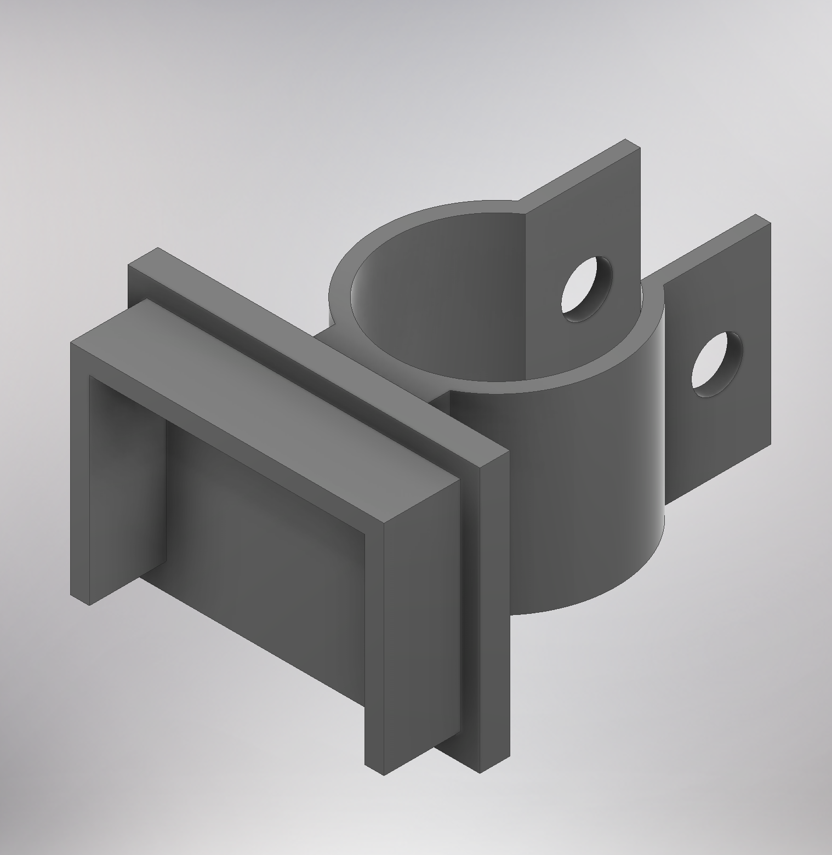
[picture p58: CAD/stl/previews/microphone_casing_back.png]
| microphone_casing_back.STL | 2 | 25 min/23 min | 5.42 |  |
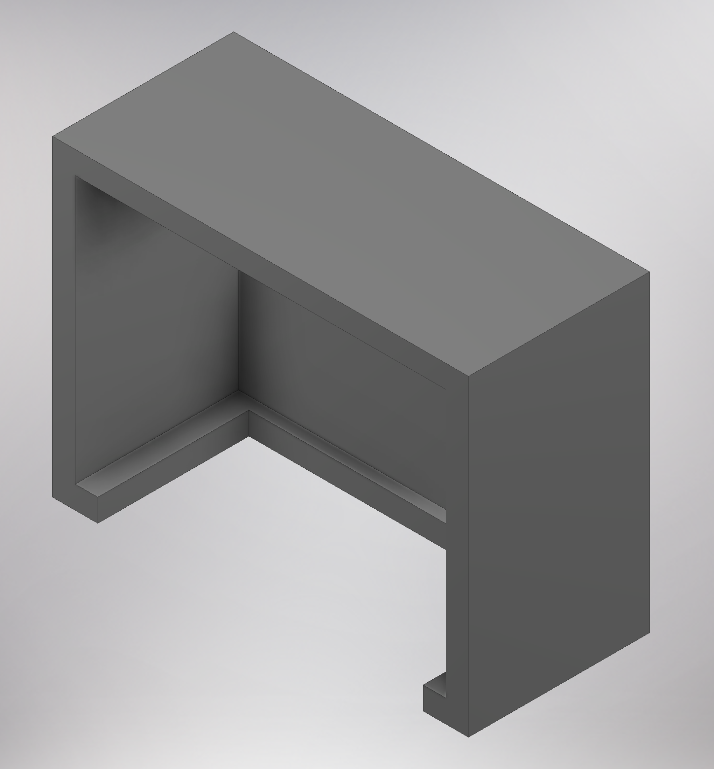
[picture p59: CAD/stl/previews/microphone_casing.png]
| microphone_casing.STL | 2 | 13 min/13 min | 2.84|  |
| **Total** | | 30 hr/23.5 hr | 571.5 |

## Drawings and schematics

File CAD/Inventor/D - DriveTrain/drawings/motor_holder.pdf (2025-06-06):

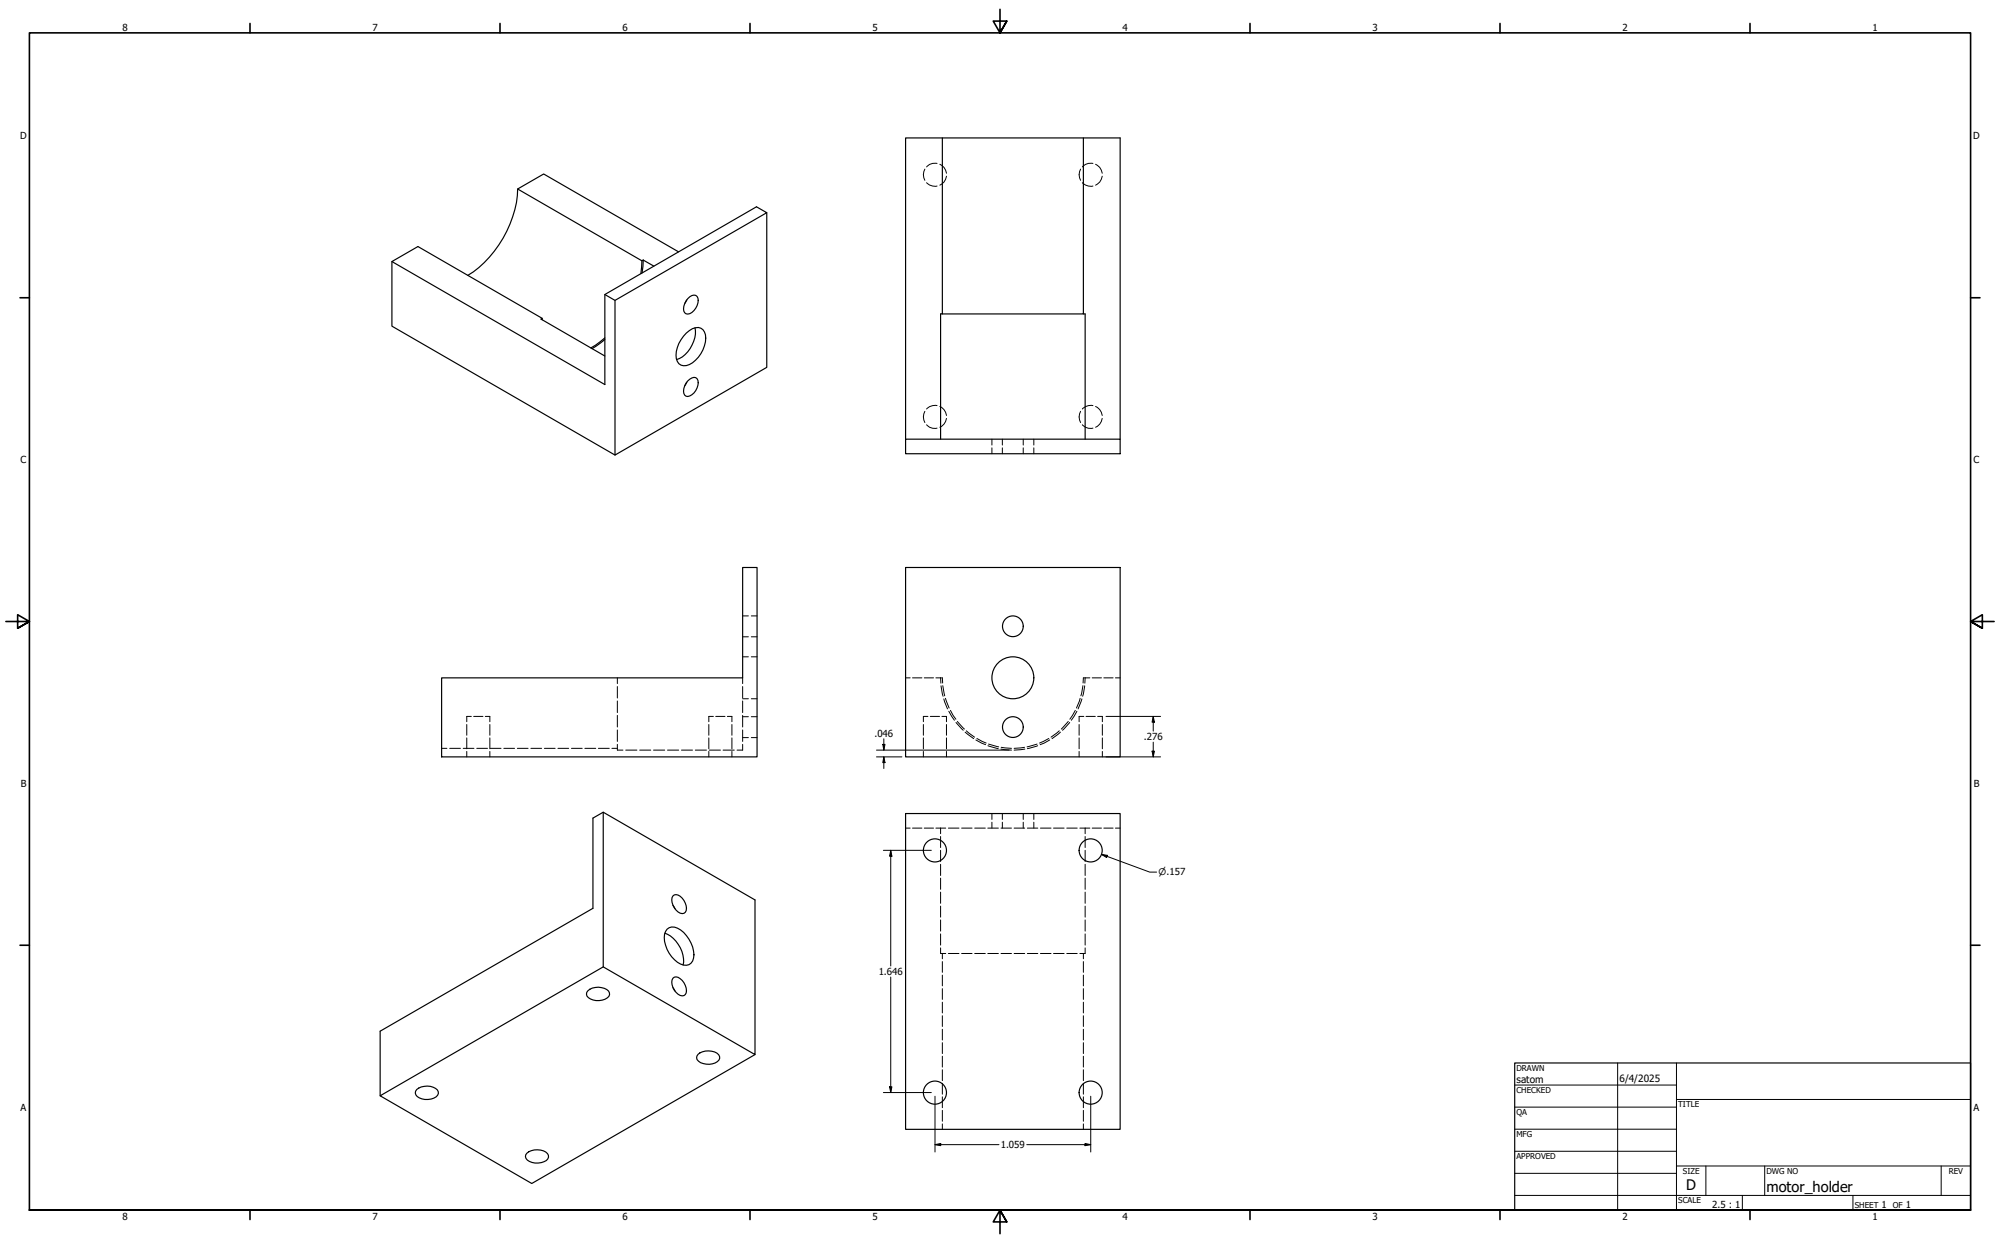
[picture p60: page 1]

DRAWN satom | 6/4/2025

CHECKED

MFG

APPROVED

SIZE D | DWG NO motor_holder | REV

SCALE 2.5 : 1 | | SHEET 1 OF 1

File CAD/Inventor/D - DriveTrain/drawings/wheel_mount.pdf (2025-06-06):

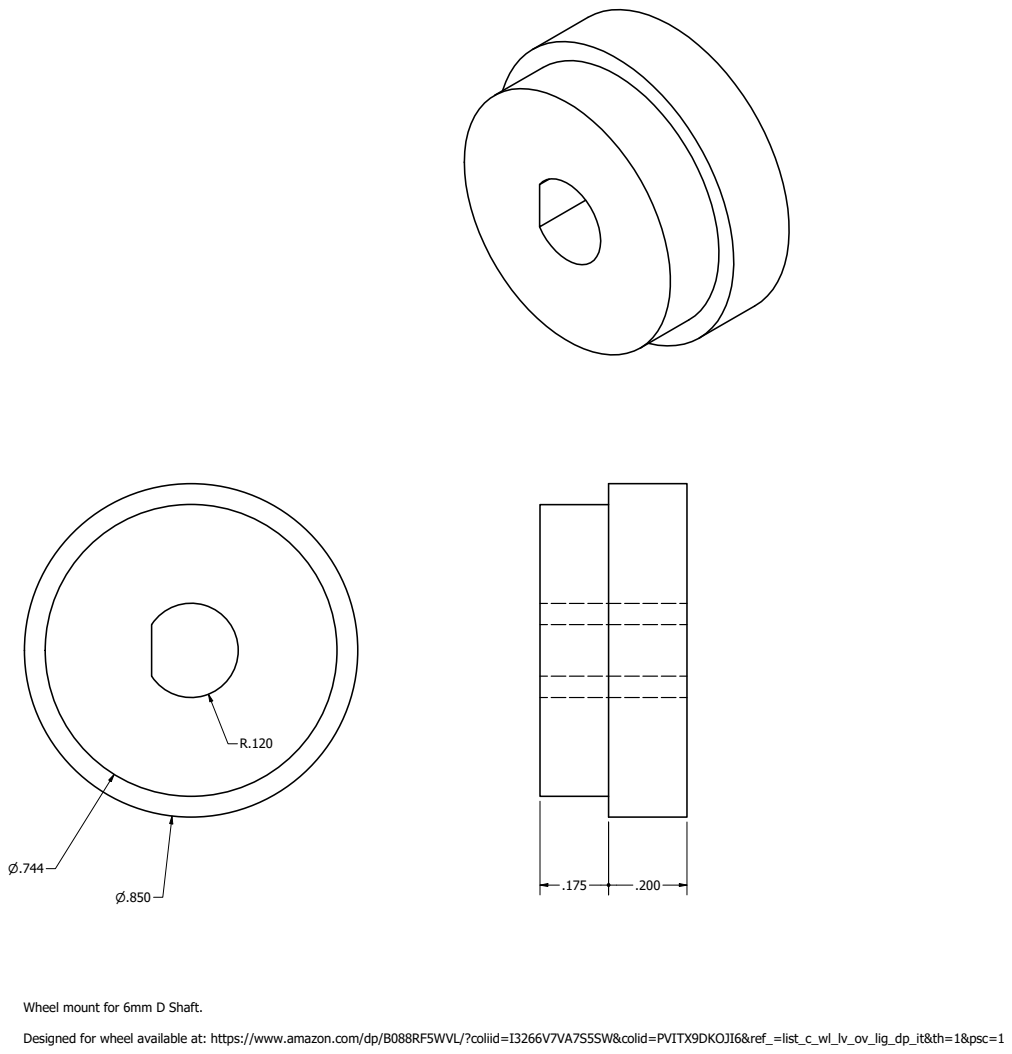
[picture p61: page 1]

Wheel mount for 6mm D Shaft.

Designed for wheel available at: https://www.amazon.com/dp/B088RF5WVL/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

DRAWN satom | 6/4/2025

CHECKED

MFG

APPROVED

SIZE D | DWG NO wheel_mount | REV

SCALE 5 : 1 | | SHEET 1 OF 1

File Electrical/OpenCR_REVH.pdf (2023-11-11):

PA0-WKUP 34 PA1 35 PA2 36 PA3 37 PA4 40 PA5 41 PA6 42 PA7 43 PA8 100 PA9 101 PA10 102 PA11 103 PA12 104 PA13 105 PA14 109 PA15 110 PB0 46 PB1 47 PB2 48 PB3 133 PB4 134 PB5 135 PB6 136 PB7 137 PB8 139 PB9 140 PB10 69 PB11 70 PB12 73 PB13 74 PB14 75 PB15 76 PC14-OSC32_IN 8 PC15-OSC32_OUT 9 PH0-OSC_IN 23 PH1-OSC_OUT 24 NRST 25 BOOT0 138 PDR_ON 143
PD0 114 PD1 115 PD2 116 PD3 117 PD4 118 PD5 119 PD6 122 PD7 123 PD8 77 PD9 78 PD10 79 PD11 80 PD12 81 PD13 82 PD14 85 PD15 86 PE0 141 PE1 142 PE2 1 PE3 2 PE4 3 PE5 4 PE6 5 PE7 58 PE8 59 PE9 60 PE10 63 PE11 64 PE12 65 PE13 66 PE14 67 PE15 68 PF0 10 PF1 11 PF2 12 PF3 13 PF4 14 PF5 15 PF6 18 PF7 19 PF8 20 PF9 21 PF10 22 PF11 49 PF12 50 PF13 53 PF14 54 PF15 55

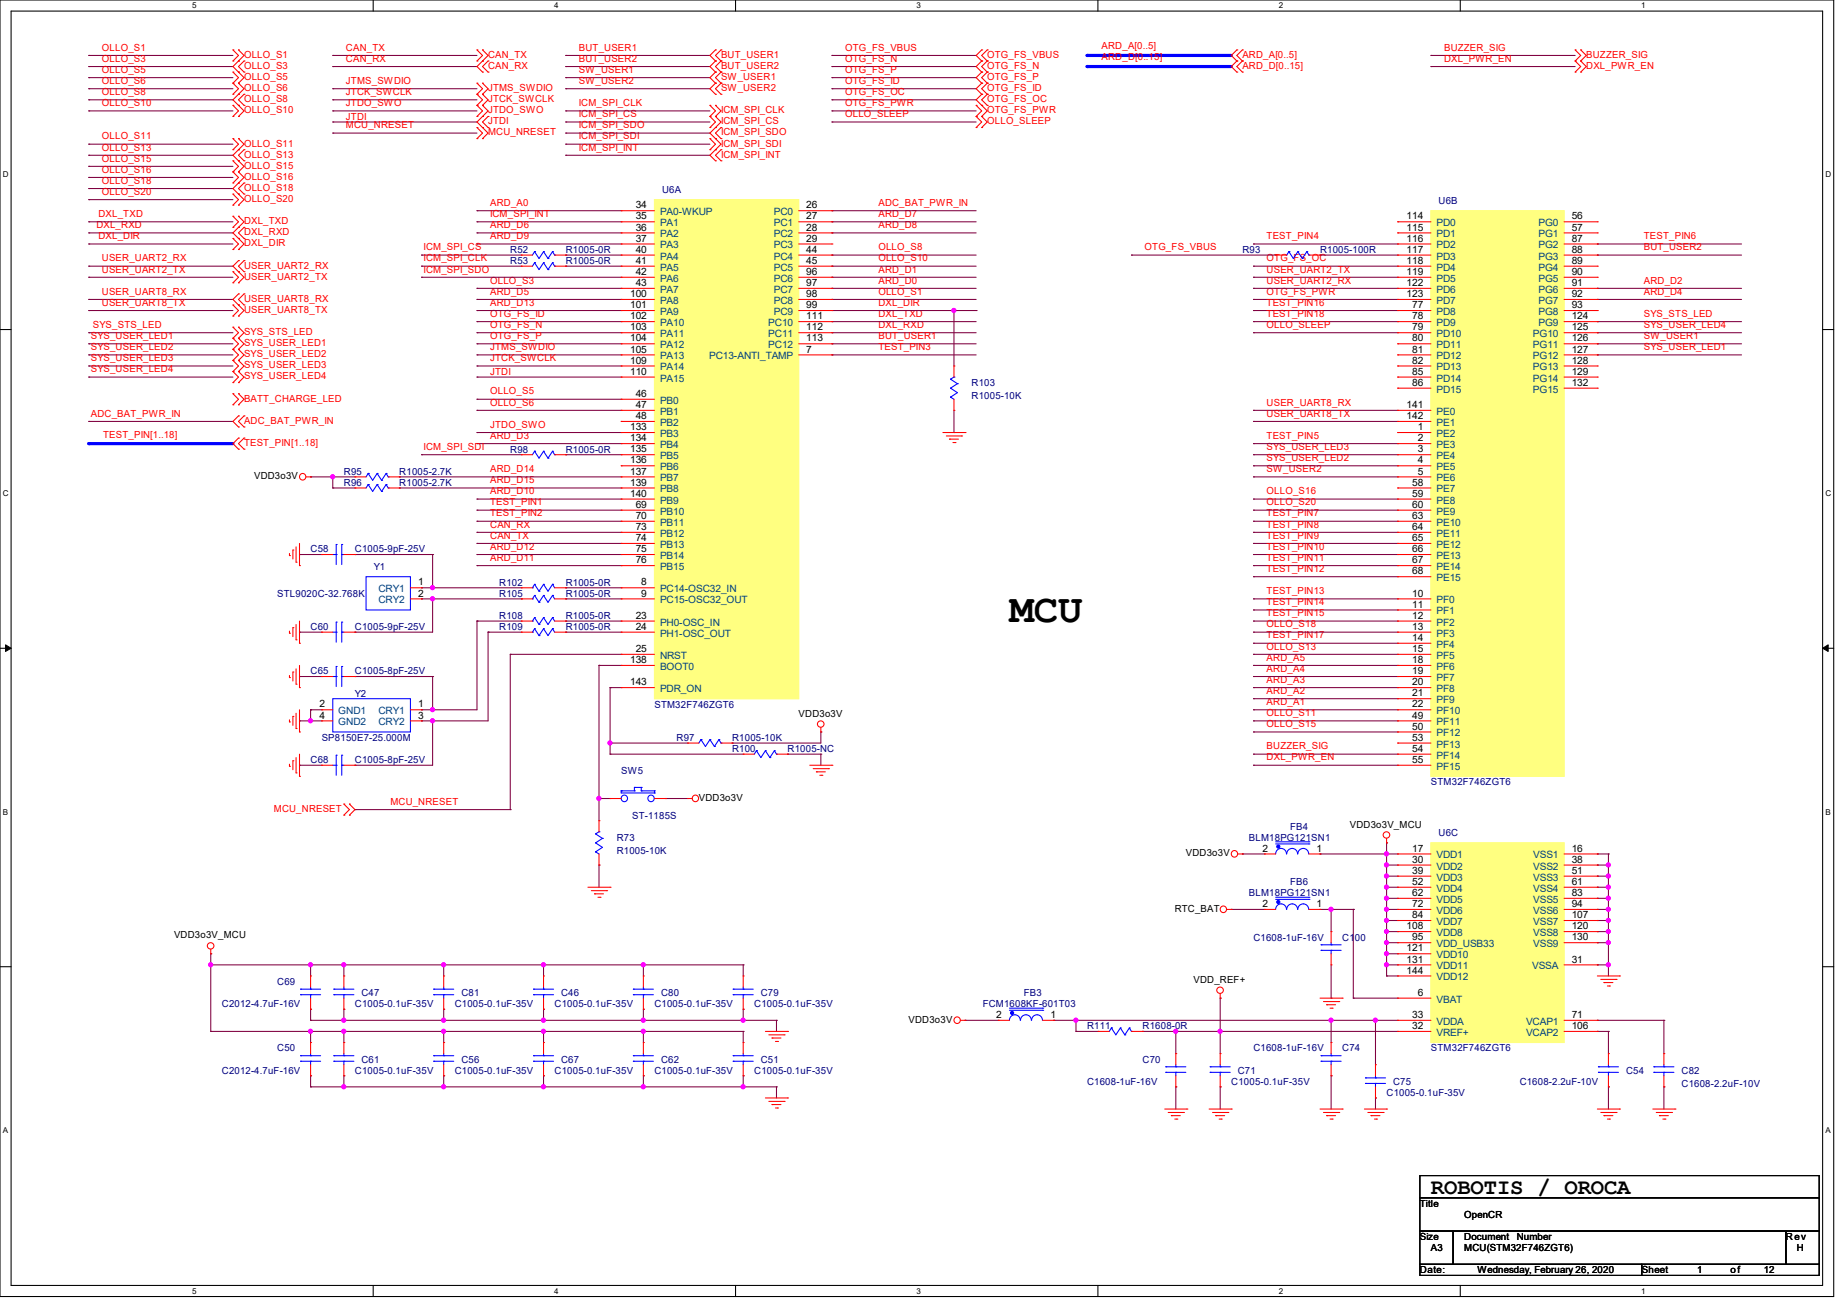
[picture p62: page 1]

# ARDUINO UNO

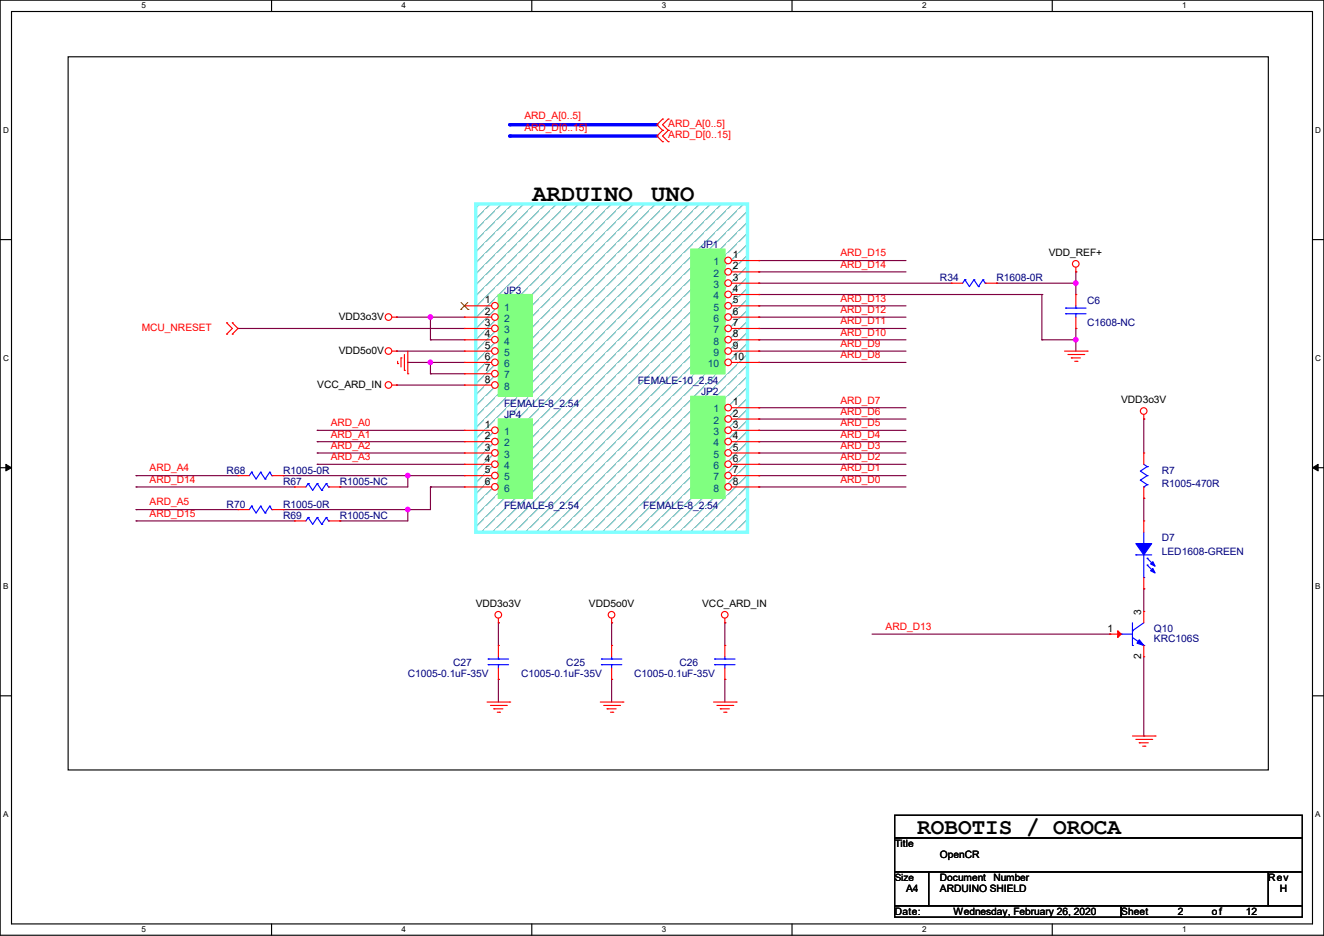
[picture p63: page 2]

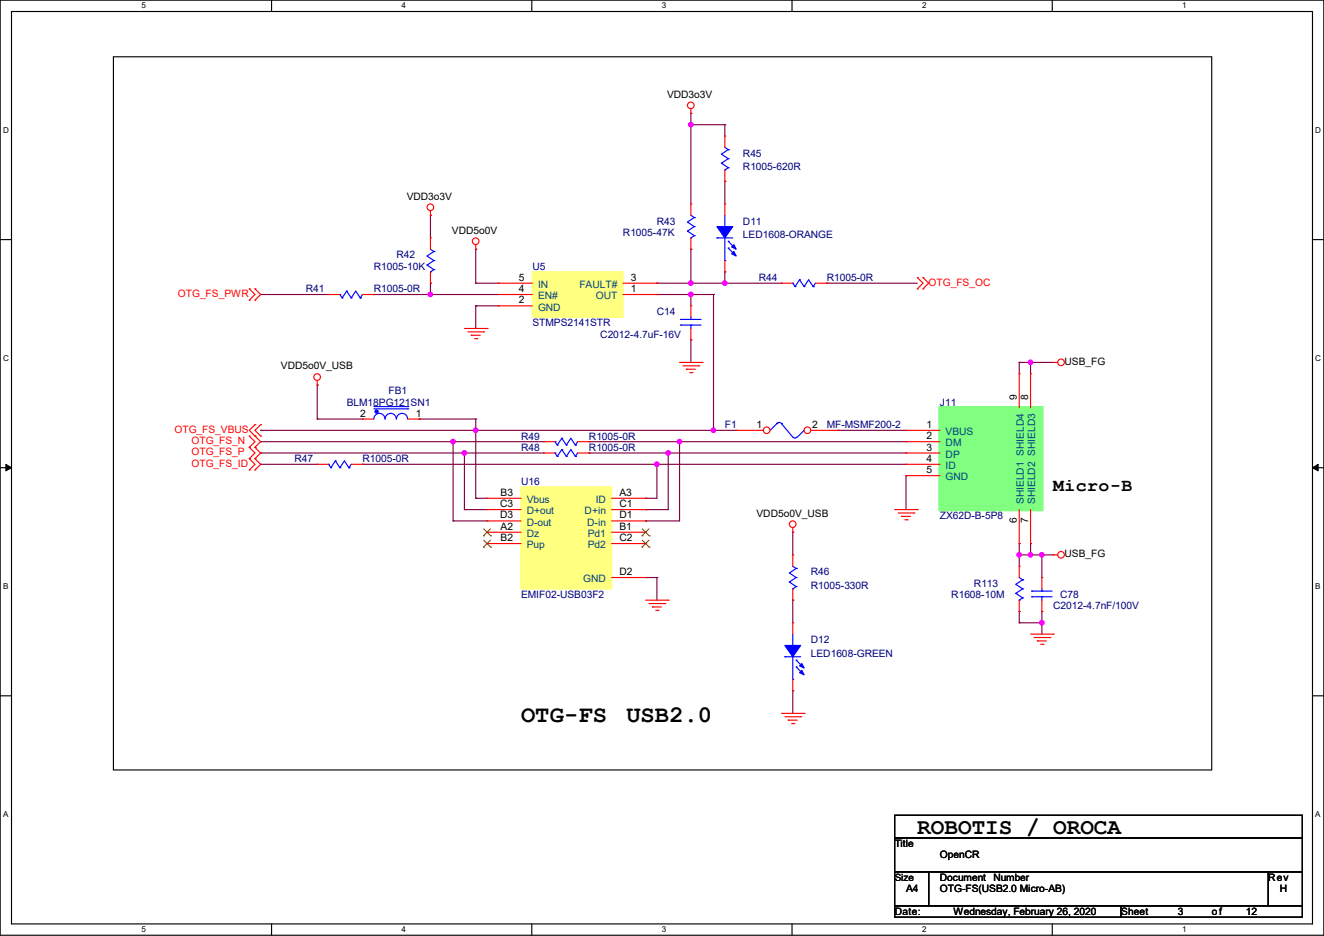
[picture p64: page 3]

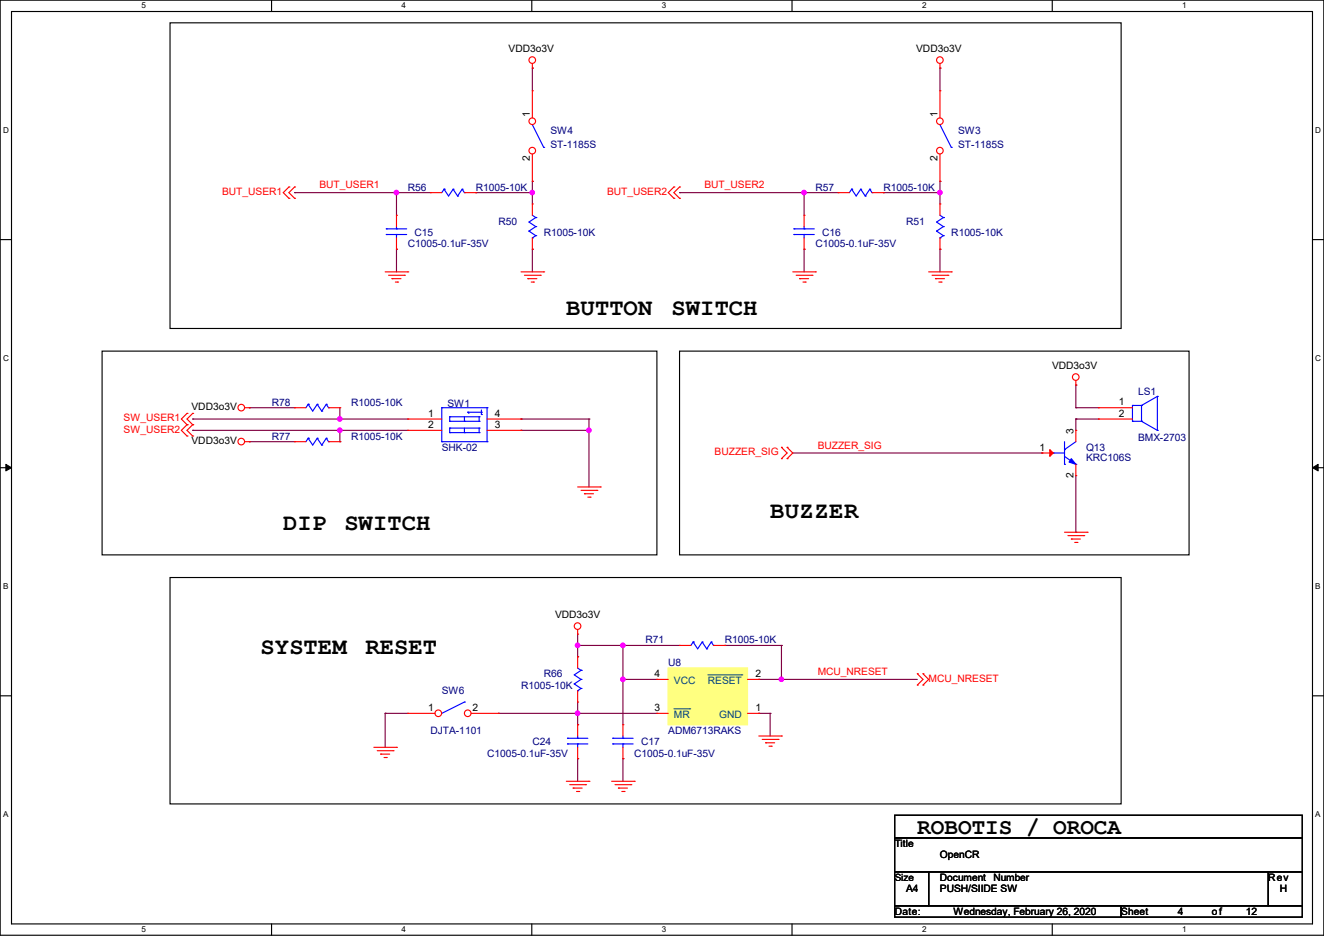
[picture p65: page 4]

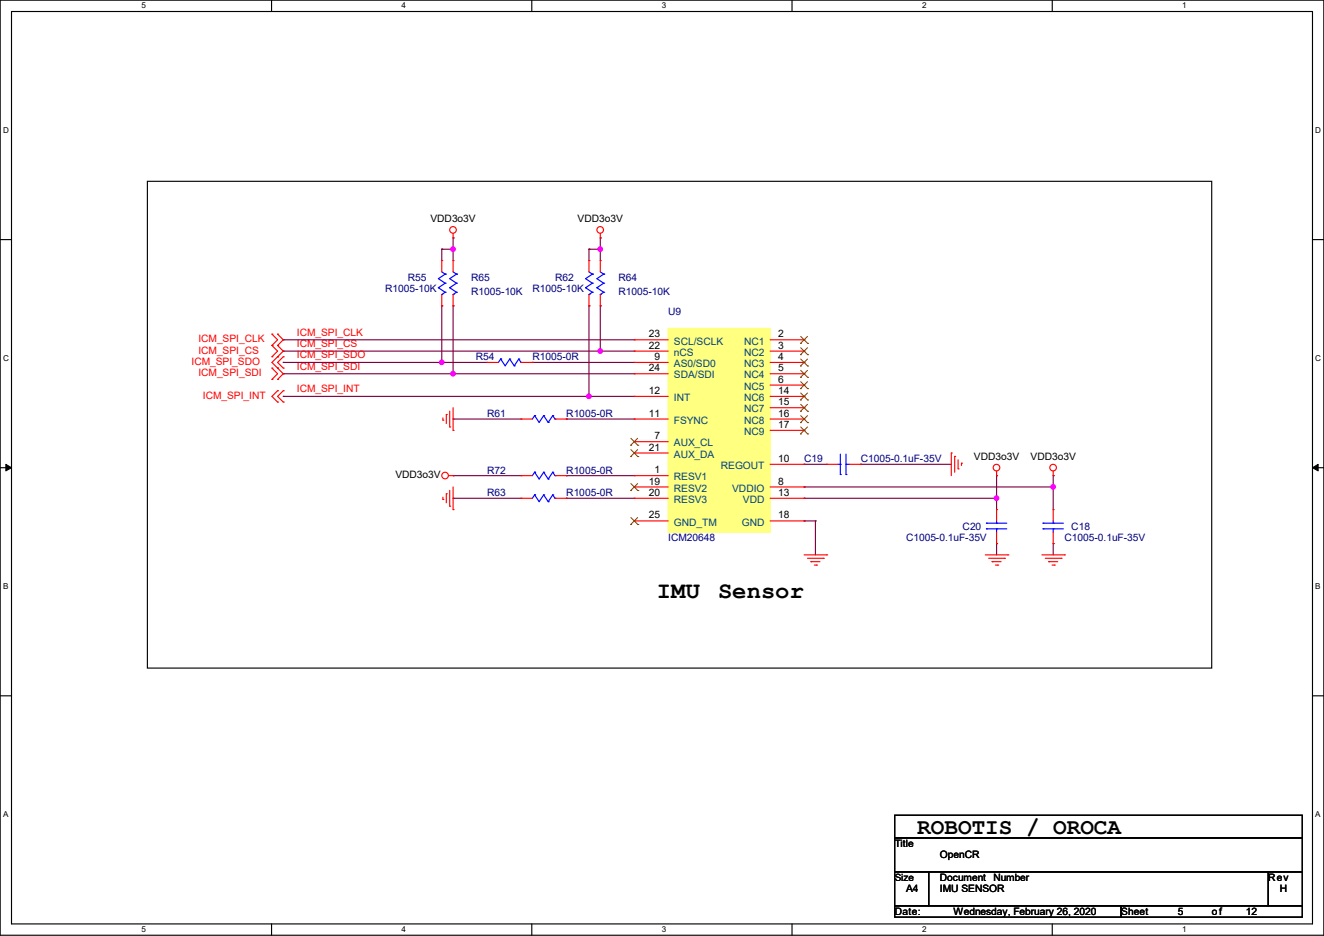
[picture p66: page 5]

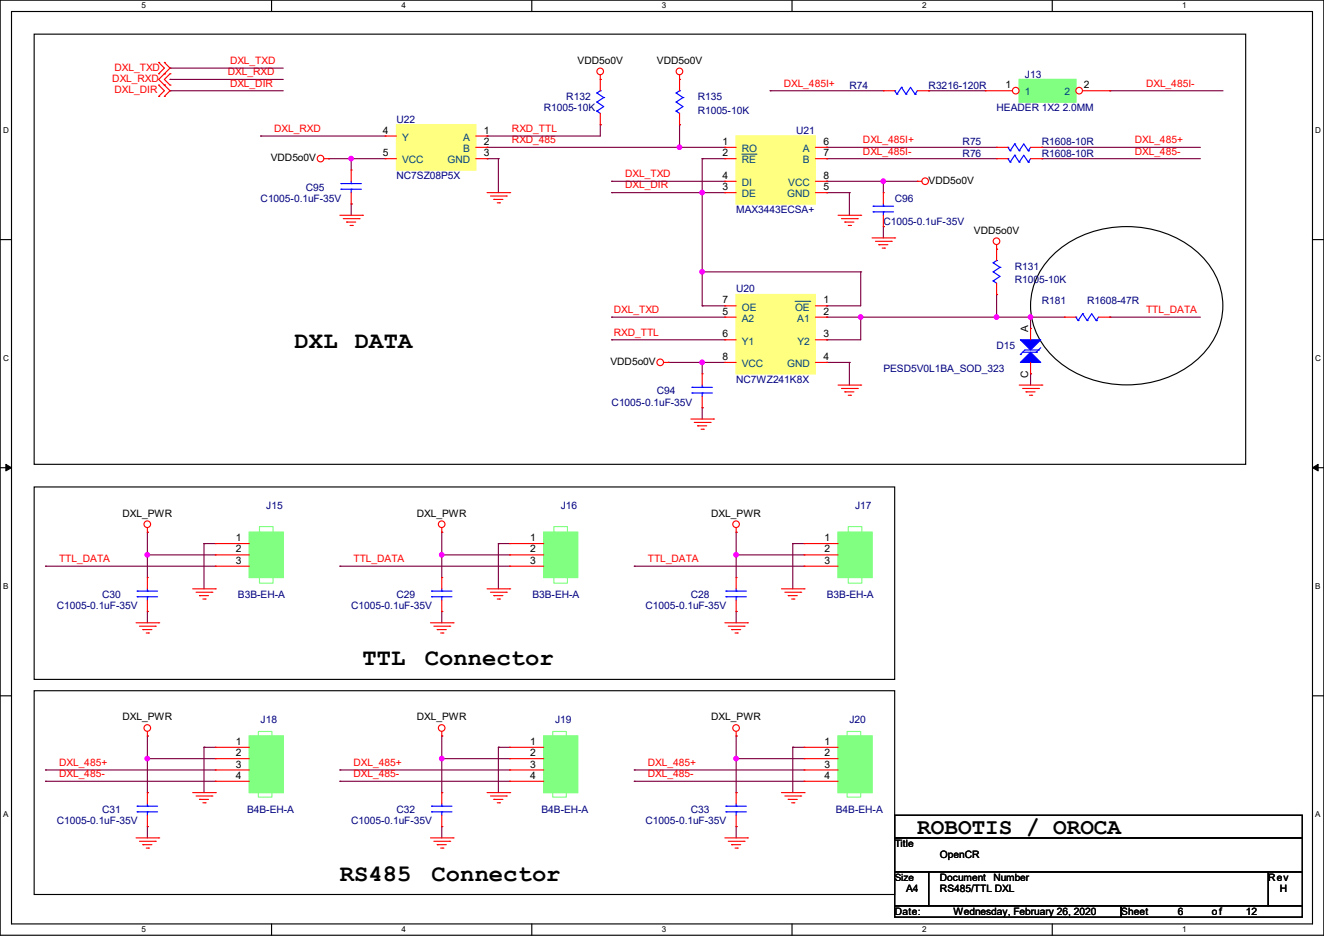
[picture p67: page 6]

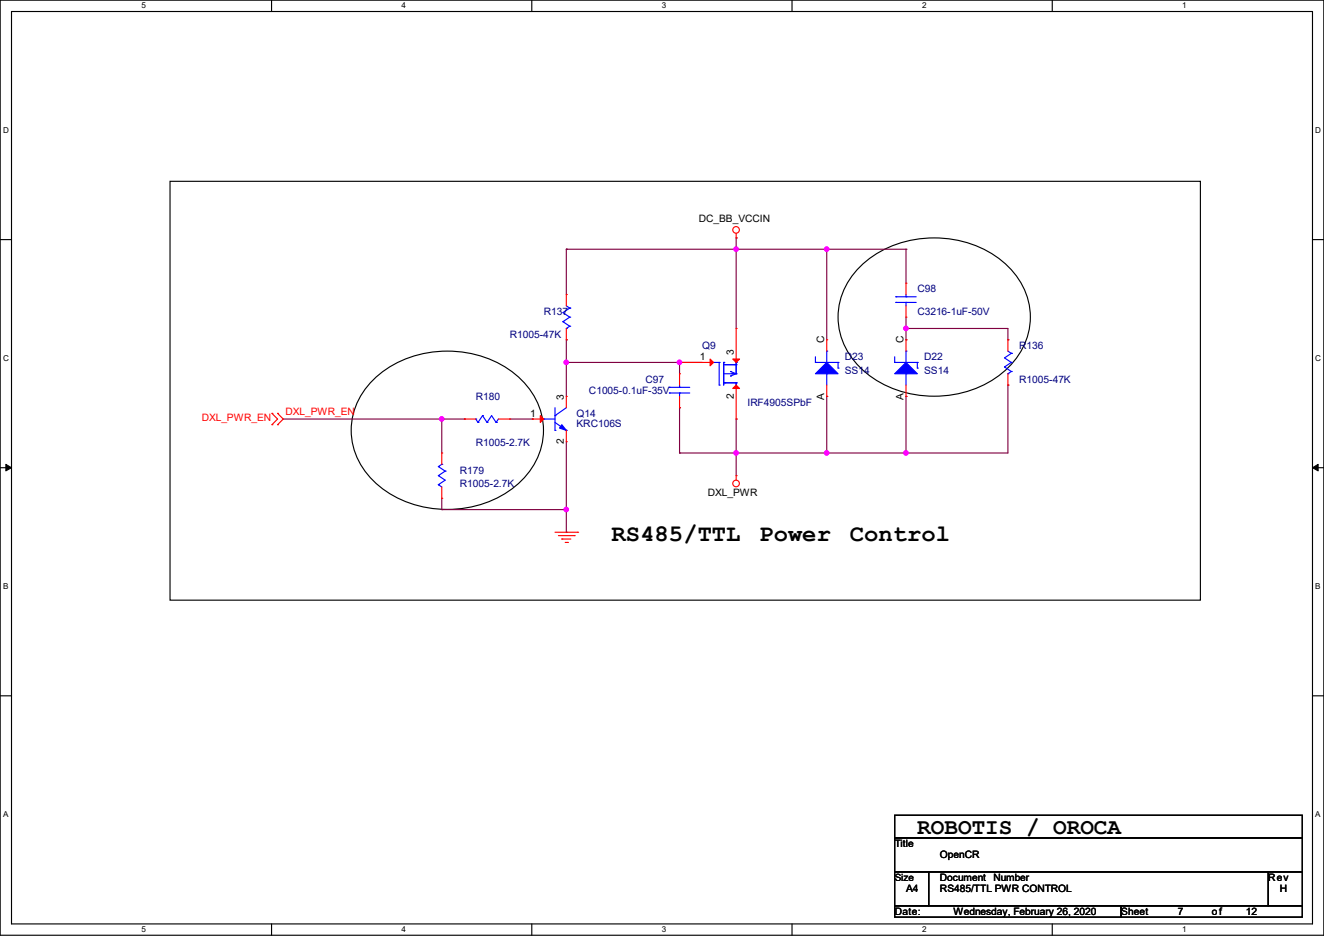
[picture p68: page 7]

# CAN

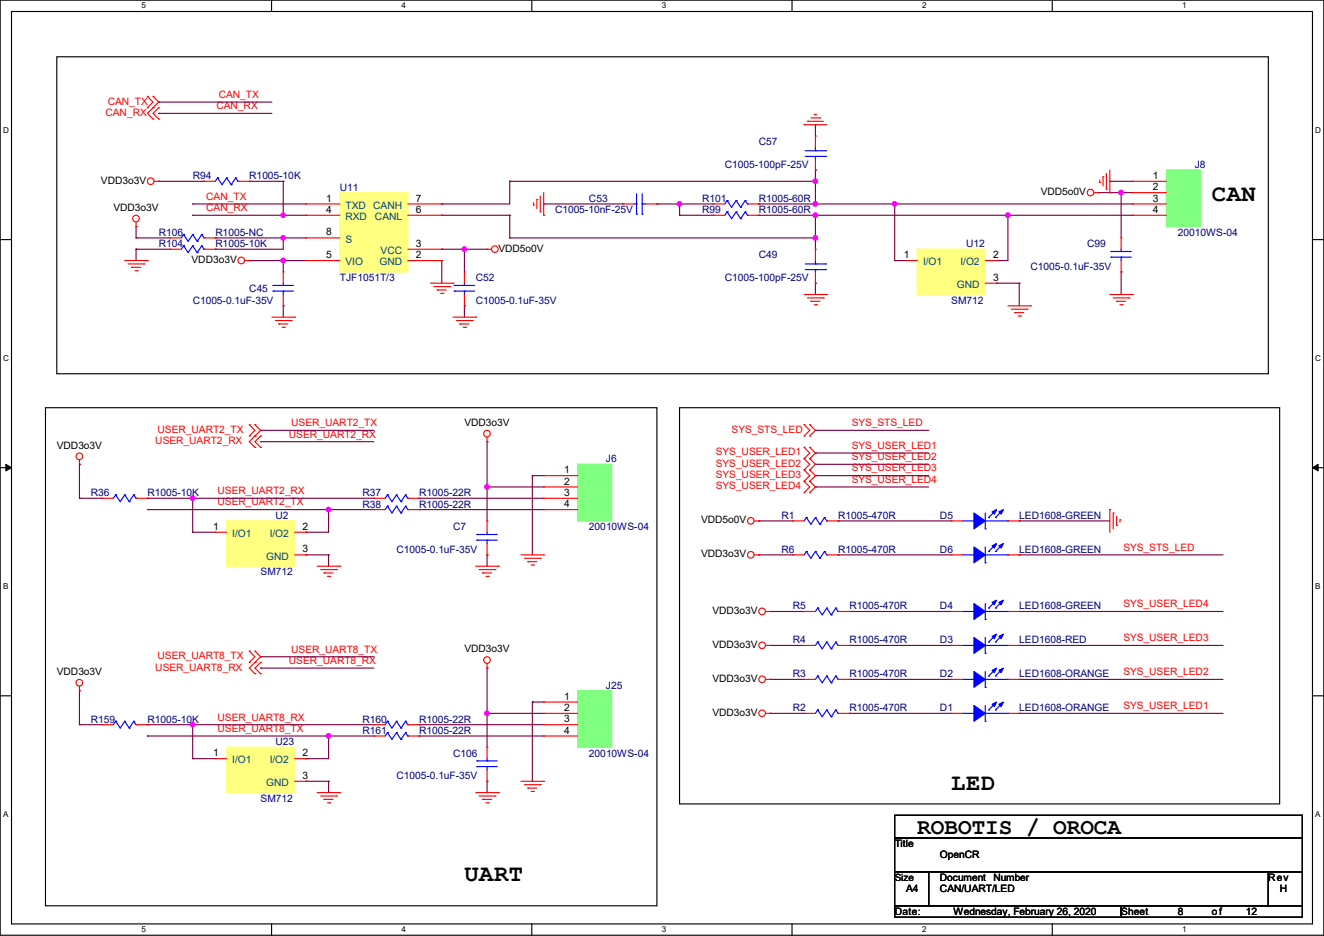
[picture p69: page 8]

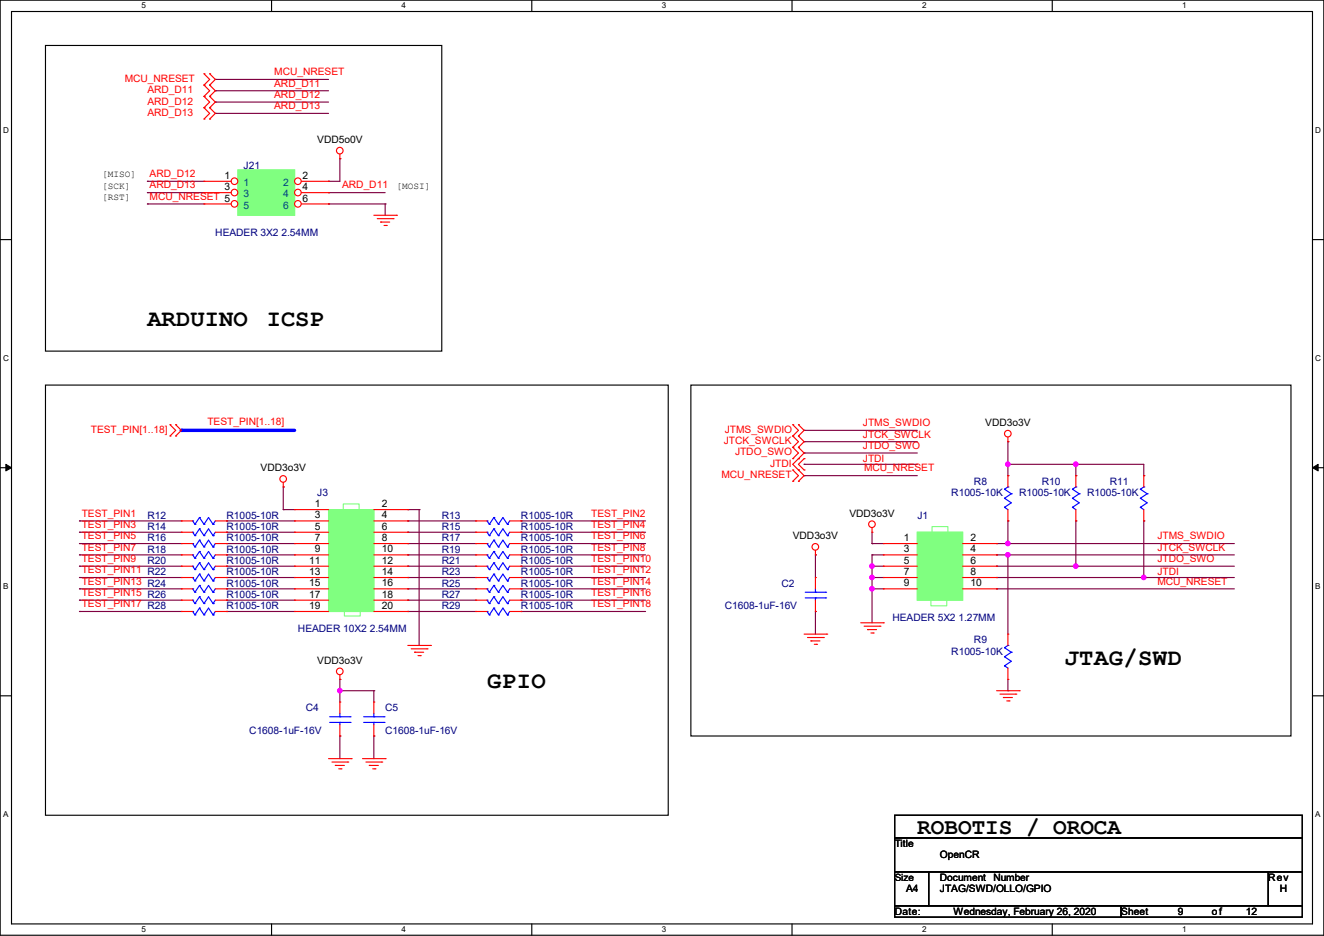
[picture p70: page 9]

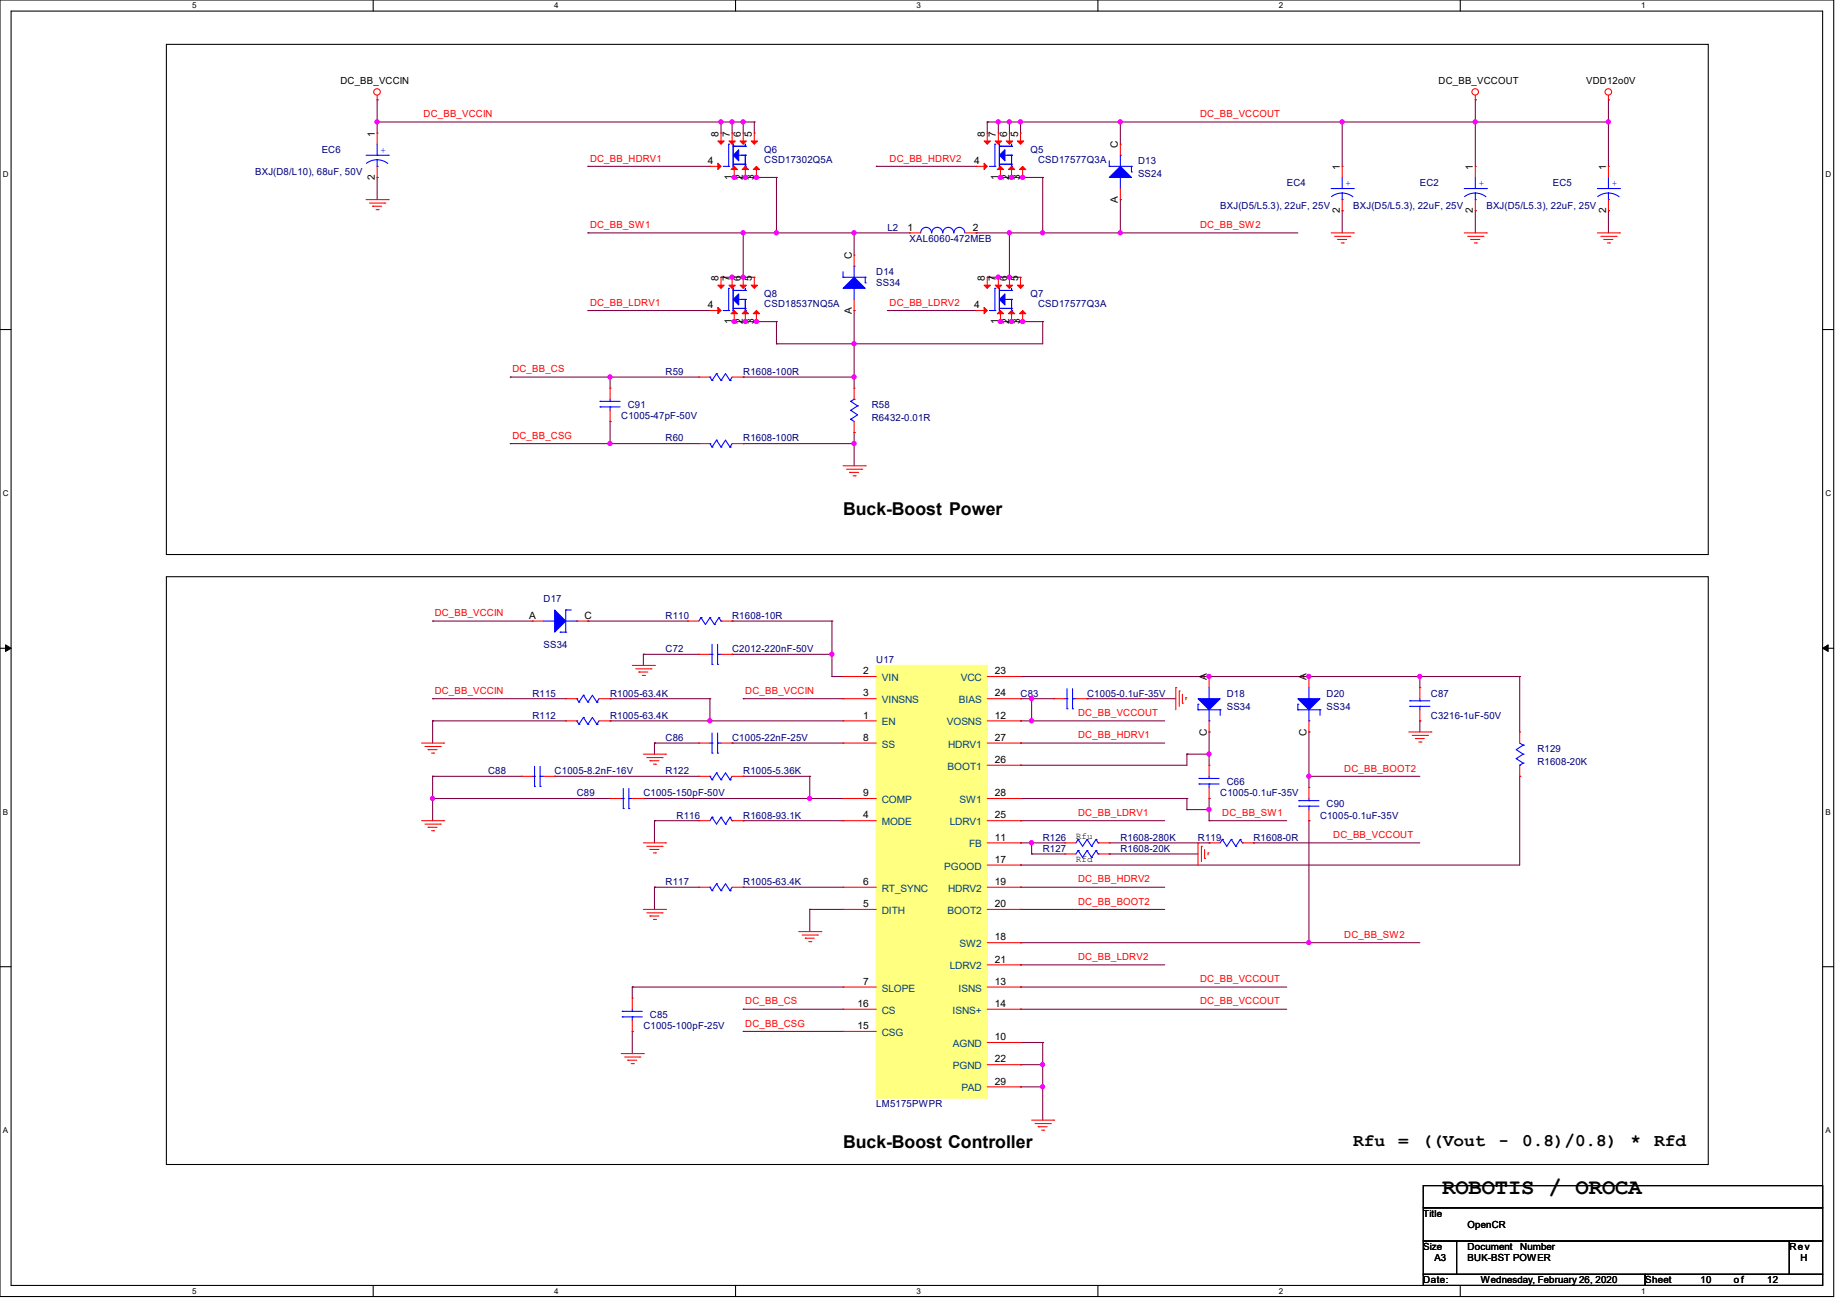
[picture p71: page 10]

### System 5V Out


2 GND 1 VIN 5 EN 4 TM


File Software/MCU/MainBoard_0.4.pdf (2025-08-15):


Id: 1/12 Title: MCU Controller File: MainBoard.kicad_sch Sheet: / satomm@stanford.edu


Id: 3/12 Title: MCU Controller File: IMU.kicad_sch Sheet: /IMU/ satomm@stanford.edu


UART5 (PIC32 PPS Mapping) TX: RB3 (0011) RX: RB5 (1000) SPI3 (PIC32 PPS Mapping) SS*: RB15 (0111 ouput, 0011 input) SCK: RB14 SDO: RB10 (0111) SDI: RB9 (0101) UART3 (General Purpose Use)

satomm@stanford.edu
Id: 4/12 Title: MCU Controller File: SPI_UART.kicad_sch Sheet: /SPI_UART/


Id: 5/12 Title: MCU Controller File: LED.kicad_sch Sheet: /LED/ satomm@stanford.edu


Id: 6/12 Title: MCU Controller File: Buttons.kicad_sch Sheet: /Buttons/ satomm@stanford.edu


Id: 7/12 Title: MCU Controller File: USB.kicad_sch Sheet: /USB/ satomm@stanford.edu


I0 - I4 Function Slow Decay: Logic low Mixed Decay: Open Fast Decay: Logic high PWM Frequency: 100 kHz max

Id: 8/12 Title: MCU Controller File: Motor.kicad_sch Sheet: /Motor/ satomm@stanford.edu


Id: 9/12 Title: MCU Controller File: OtherSensors.kicad_sch Sheet: /OtherSensors/ satomm@stanford.edu


Id: 10/12 Title: MCU Controller File: GPS.kicad_sch Sheet: /GPS/ satomm@stanford.edu


Id: 11/12 Title: MCU Controller File: GPIO.kicad_sch Sheet: /GPIO/ satomm@stanford.edu


3 3 | 4 4
5 5 | 6 6
7 7 | 8 8
9 9 | 10

Molex + Switch Male, DigiKey P/N: WM4622-ND

Inputs:
1) Motor Battery: 2x NiMH Battery, 7.2 V Each
2) Battery for MCU: 5 V

Id: 12/12 Title: MCU Controller File: power.kicad_sch Sheet: /Power/ satomm@stanford.edu


satomm@stanford.edu
Id: 12/12 Title: MCU Controller File: Memory.kicad_sch Sheet: /Memory/

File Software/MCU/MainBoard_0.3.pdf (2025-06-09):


0.1 uF H4 MountingHole H3 MountingHole H1 MountingHole H2 MountingHole

Id: 1/12 Title: MCU Controller File: MainBoard.kicad_sch Sheet: / satomm@stanford.edu


Id: 3/12 Title: MCU Controller File: IMU.kicad_sch Sheet: /IMU/ satomm@stanford.edu


satomm@stanford.edu
Id: 4/12 Title: MCU Controller File: SPI_UART.kicad_sch Sheet: /SPI_UART/


Id: 5/12 Title: MCU Controller File: LED.kicad_sch Sheet: /LED/ satomm@stanford.edu


Id: 6/12 Title: MCU Controller File: Buttons.kicad_sch Sheet: /Buttons/ satomm@stanford.edu


Id: 7/12 Title: MCU Controller File: USB.kicad_sch Sheet: /USB/ satomm@stanford.edu


Placed close to motor driver Motor Voltage: 8.2 V min
Vdrive C24

Chopping Current at 100% Scale Chopping Current at 100% Scale VREF Voltage: 1 V min

Current Sensing Resistor Surface Mount Low Inductance Rated for high enough power: Irms^2 * R

PWM Frequency: 100 kHz max Slow Decay: Logic low Mixed Decay: Open Fast Decay: Logic high

Id: 8/12 Title: MCU Controller File: Motor.kicad_sch Sheet: /Motor/ satomm@stanford.edu


Id: 9/12 Title: MCU Controller File: OtherSensors.kicad_sch Sheet: /OtherSensors/ satomm@stanford.edu


Id: 10/12 Title: MCU Controller File: GPS.kicad_sch Sheet: /GPS/ satomm@stanford.edu


Id: 11/12 Title: MCU Controller File: GPIO.kicad_sch Sheet: /GPIO/ satomm@stanford.edu


3.3V Supply C14 5 5 | 6 6

7 7 | 8 8
9 9 | 10

Molex + Switch Male, DigiKey P/N: WM4622-ND

3 3 | 4 4
5 5 | 6 6

1) Motor Battery: 2x NiMH Battery, 7.2 V Each
2) Battery for MCU: 5 V

Id: 12/12 Title: MCU Controller File: power.kicad_sch Sheet: /Power/ satomm@stanford.edu


satomm@stanford.edu
Id: 12/12 Title: MCU Controller File: Memory.kicad_sch Sheet: /Memory/

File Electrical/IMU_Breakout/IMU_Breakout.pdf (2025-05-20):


Id: 1/1 Title: Test sheet File: IMU_Breakout.kicad_sch Sheet: / satomm@stanford.edu

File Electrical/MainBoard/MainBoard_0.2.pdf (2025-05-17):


Figure out antenna Bumper/

Vdrive Power File: Power.kicad_sch
Power

Id: 1/12 Title: MCU Controller File: MainBoard.kicad_sch Sheet: / satomm@stanford.edu


Inputs:
1) Motor Battery: 2x NiMH Battery, 7.2 V Each
2) Battery For Jetson: 12 V
3) Battery for MCU: 5 V

Id: 2/12 Title: MCU Controller File: Power.kicad_sch Sheet: /Power/ satomm@stanford.edu


Id: 3/12 Title: MCU Controller File: IMU.kicad_sch Sheet: /IMU/ satomm@stanford.edu


Primary use is for Jetson SDI2/SDA4 SDO2/SCL4

satomm@stanford.edu
Id: 4/12 Title: MCU Controller File: SPI_UART.kicad_sch Sheet: /SPI_UART/


Id: 5/12 Title: MCU Controller File: LED.kicad_sch Sheet: /LED/ satomm@stanford.edu


Id: 6/12 Title: MCU Controller File: Buttons.kicad_sch Sheet: /Buttons/ satomm@stanford.edu


TX Indicator RX Indicator GND GND

Id: 7/12 Title: MCU Controller File: USB.kicad_sch Sheet: /USB/ satomm@stanford.edu


Chopping Current at 100% Scale Current Sensing Resistor Surface Mount Low Inductance Rated for high enough power: Irms^2 * R

Id: 8/12 Title: MCU Controller File: Motor.kicad_sch Sheet: /Motor/ satomm@stanford.edu


Id: 9/12 Title: MCU Controller File: OtherSensors.kicad_sch Sheet: /OtherSensors/ satomm@stanford.edu


Id: 10/12 Title: MCU Controller File: GPS.kicad_sch Sheet: /GPS/ satomm@stanford.edu


Id: 11/12 Title: MCU Controller File: GPIO.kicad_sch Sheet: /GPIO/ satomm@stanford.edu


satomm@stanford.edu
Id: 12/12 Title: MCU Controller File: Memory.kicad_sch Sheet: /Memory/

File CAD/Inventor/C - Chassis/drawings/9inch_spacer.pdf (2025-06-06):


DRAWN satom | 6/4/2025

CHECKED

MFG

APPROVED

SIZE D | DWG NO 9inch_spacer | REV

SCALE 1 : 1 | | SHEET 1 OF 1

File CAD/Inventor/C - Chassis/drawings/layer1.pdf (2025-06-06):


DRAWN satom | 6/4/2025

CHECKED

MFG

APPROVED

SIZE D | DWG NO layer1 | REV

SCALE 1 : 1 | | SHEET 1 OF 1


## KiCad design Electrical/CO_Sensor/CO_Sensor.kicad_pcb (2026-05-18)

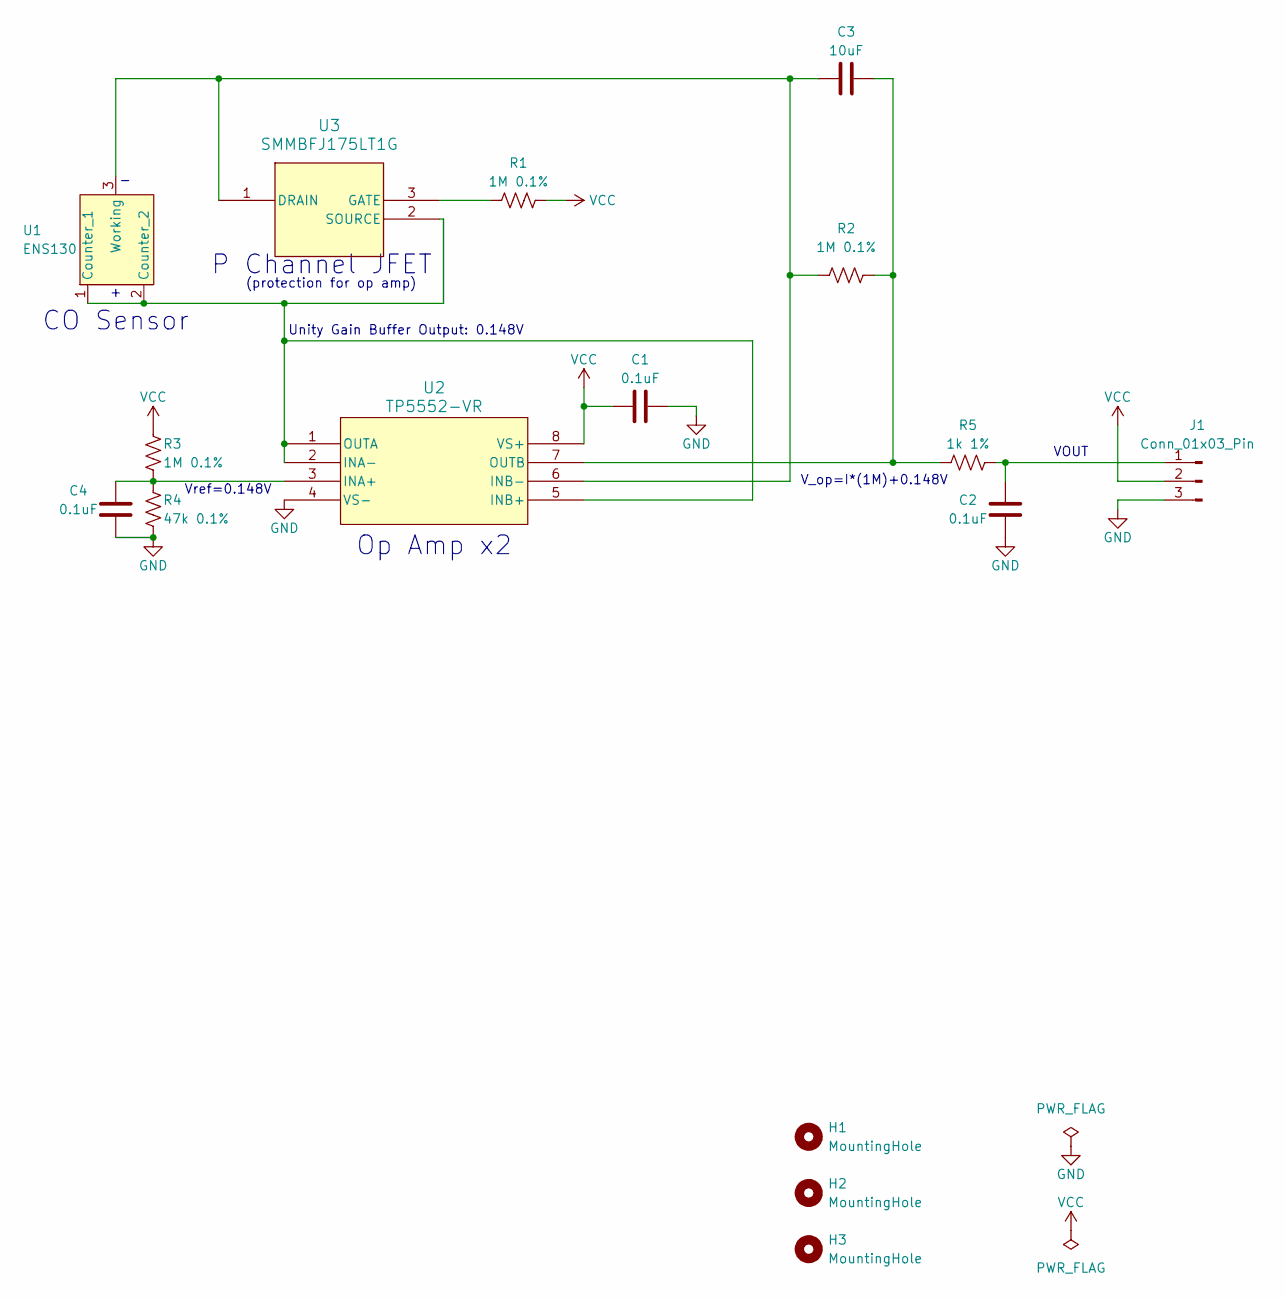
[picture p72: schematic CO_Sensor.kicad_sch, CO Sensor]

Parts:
C1, C2, C4: 0.1uF; C_0805_2012Metric_Pad1.18x1.45mm_HandSolder; Mfr P/N CL21B104KBCNNNC
C3: 10uF; C_0805_2012Metric_Pad1.18x1.45mm_HandSolder; Mfr P/N CL21A106KOQNNNE
H1, H2, H3: MountingHole; MountingHole_3.2mm_M3
J1: Conn_01x03_Pin; PinHeader_1x03_P2.54mm_Vertical
R1, R2, R3: 1M 0.1%; R_0805_2012Metric_Pad1.20x1.40mm_HandSolder; Mfr P/N ERA-6AEB105V
R4: 47k 0.1%; R_0805_2012Metric_Pad1.20x1.40mm_HandSolder; Mfr P/N ERA-6AEB473V
R5: 1k 1%; R_0805_2012Metric_Pad1.20x1.40mm_HandSolder; Mfr P/N RMCF0805FT1K00
U1: ENS130; Mfr P/N ENS130
U2: TP5552-VR; VS1MSOP-8-A_TPK-M; Mfr P/N TP5552-VR
U3: SMMBFJ175LT1G; SOT-23_ONS-M; Mfr P/N SMMBFJ175LT1G

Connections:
GND: C1.2, C2.1, C4.1, J1.3, R4.1, U2.4 (VS-)
unnamed: C2.2, J1.1, R5.1
unnamed: U1.1 (Counter_1), U1.2 (Counter_2), U2.1 (OUTA), U2.2 (INA-), U2.5 (INB+), U3.2 (SOURCE)
unnamed: C3.1, R2.1, U1.3 (Working), U2.6 (INB-), U3.1 (DRAIN)
unnamed: C4.2, R3.1, R4.2, U2.3 (INA+)
unnamed: C3.2, R2.2, R5.2, U2.7 (OUTB)
unnamed: R1.1, U3.3 (GATE)
VCC: C1.1, J1.2, R1.2, R3.2, U2.8 (VS+)

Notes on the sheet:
Unity Gain Buffer Output: 0.148V
CO Sensor
P Channel JFET
Op Amp x2
Vref=0.148V
(protection for op amp)
VOUT
V_op=I*(1M)+0.148V

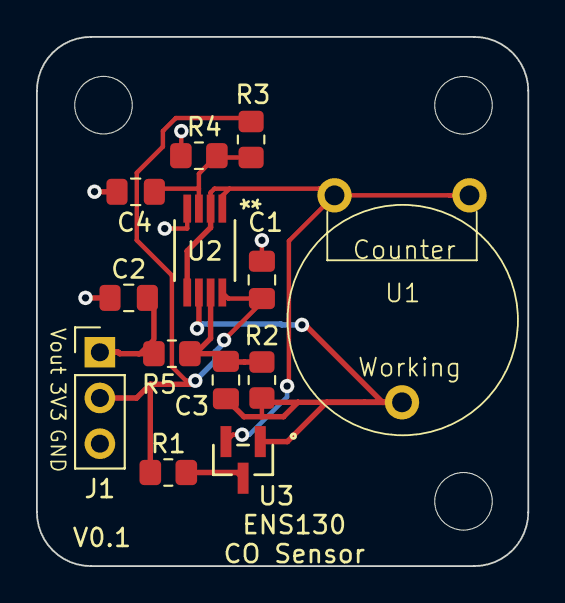
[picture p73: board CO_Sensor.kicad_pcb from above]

Board: 2 copper layers, 27.3 x 29.4 mm, 16 parts (0 on the bottom side), 8 nets.

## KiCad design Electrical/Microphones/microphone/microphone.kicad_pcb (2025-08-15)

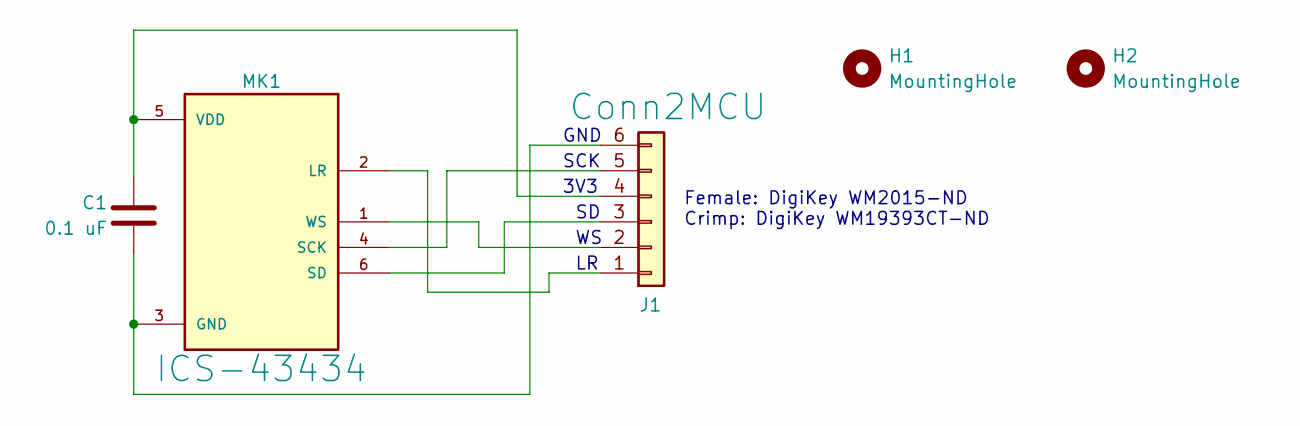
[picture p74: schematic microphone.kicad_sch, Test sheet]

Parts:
C1: 0.1 uF; C_0805_2012Metric_Pad1.18x1.45mm_HandSolder; Mfr P/N CL21B104KBCNNNC
H1, H2: MountingHole; MountingHole_3.2mm_M3
J1: Conn2MCU; CONN_22-05-3061_MOL; Mfr P/N 0022053061
MK1: ICS-43434; MIC_ICS-43434; Mfr P/N ICS-43434

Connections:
unnamed: J1.1, MK1.2 (LR)
unnamed: J1.2, MK1.1 (WS)
unnamed: J1.3, MK1.6 (SD)
unnamed: C1.1, J1.4, MK1.5 (VDD)
unnamed: J1.5, MK1.4 (SCK)
unnamed: C1.2, J1.6, MK1.3 (GND)

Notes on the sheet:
GND
Female: DigiKey WM2015-ND Crimp: DigiKey WM19393CT-ND
3V3
SCK

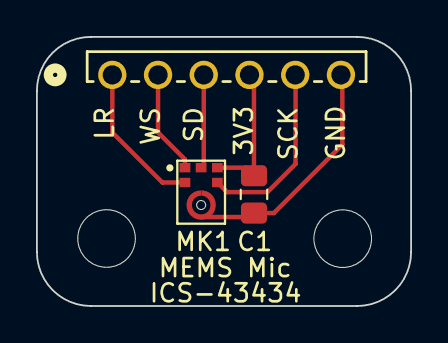
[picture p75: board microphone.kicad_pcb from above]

Board: 2 copper layers, 20.8 x 15.0 mm, 5 parts (0 on the bottom side), 6 nets.

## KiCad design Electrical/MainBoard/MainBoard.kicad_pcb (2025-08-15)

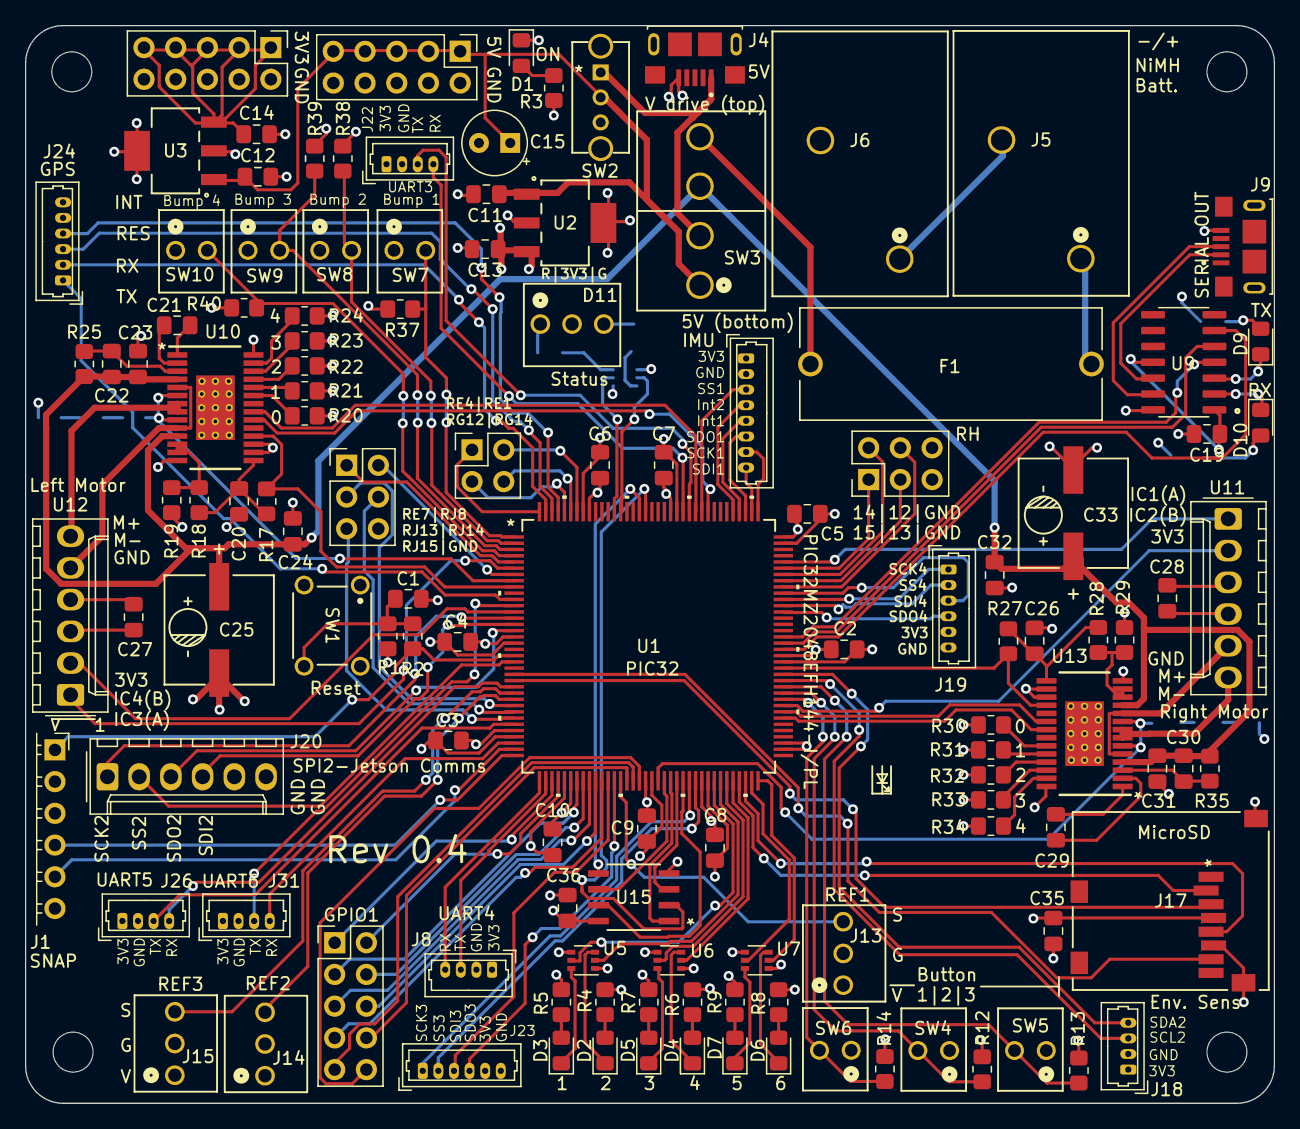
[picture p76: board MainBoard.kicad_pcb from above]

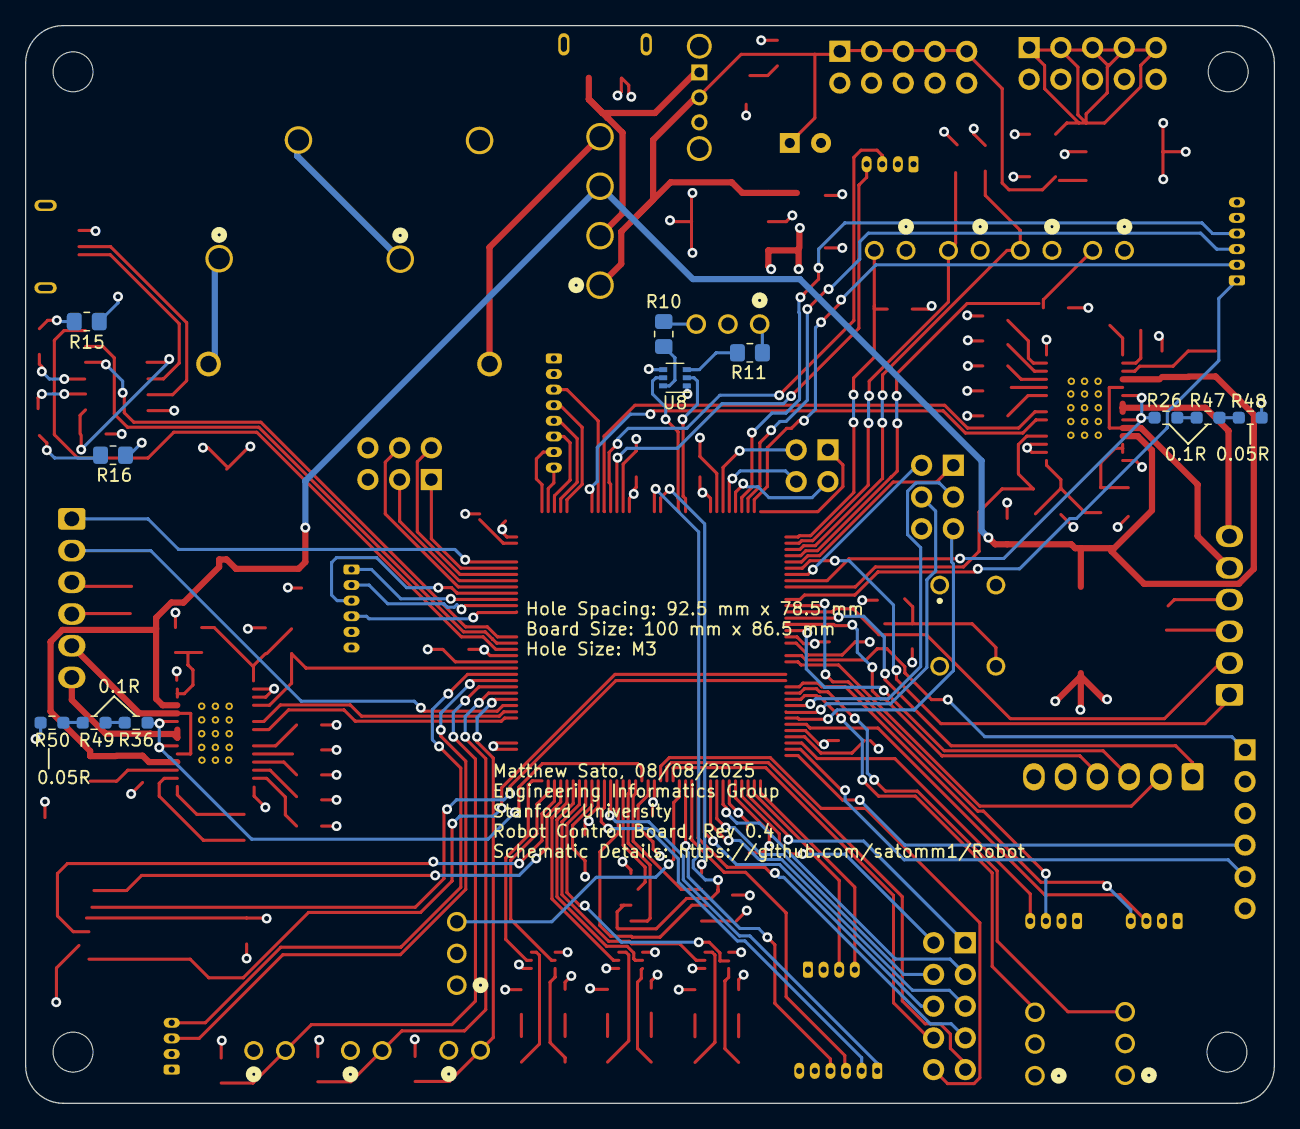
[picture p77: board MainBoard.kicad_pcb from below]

Board: 4 copper layers, 100.0 x 86.3 mm, 139 parts (11 on the bottom side), 162 nets.

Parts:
C1, C2, C3, C4, C5, C6, C7, C8, C9, C10, C19, C22, C23, C24, C27, C28, C30, C31, C32, C35, C36: 0.1 uF; C_0805_2012Metric_Pad1.18x1.45mm_HandSolder
C11, C12, C13, C14: 4.7 uF; C_0805_2012Metric_Pad1.18x1.45mm_HandSolder
C15: 10 uF; CP_Radial_Tantal_D5.0mm_P2.50mm
C20, C26: 0.47 uF; C_0805_2012Metric_Pad1.18x1.45mm_HandSolder
C21, C29: 0.01 uF; C_0805_2012Metric_Pad1.18x1.45mm_HandSolder
C25, C33: 100 uF; PCAP_8x10-ELECT_NCA-M
D1, D2, D3, D4, D5, D6, D7, D9, D10: LED; LED_0805_2012Metric_Pad1.15x1.40mm_HandSolder
D11: Status_LED; CONN3_22232031_MOL
F1: 5A Fuse; FUSE_4628
H1, H2, H3, H4: MountingHole; MountingHole_3.2mm_M3
J1: SNAP Program; PinSocket_1x06_P2.54mm_Horizontal
J2: 3.3V Supply; PinHeader_2x05_P2.54mm_Vertical
J3: 5V Supply; PinHeader_2x05_P2.54mm_Vertical
J4, J9: USB_B_Micro; AMPHENOL_10118193-0001LF
J5, J6: Battery1; CONN_1017514
J7: GPIO1; PinHeader_2x05_P2.54mm_Vertical
J8, J18, J22, J26, J31: Conn_01x04; Molex_PicoBlade_53047-0410_1x04_P1.25mm_Vertical
J13, J14, J15: Refl_PCB_Connect; CONN3_22232031_MOL
J16, J21: Conn_02x03_Odd_Even; PinHeader_2x03_P2.54mm_Vertical
J17: MEM2061-01-188-00-A; MEM2061-01-188-00-A_GCT
J19, J23, J24: Conn_01x06; Molex_PicoBlade_53047-0610_1x06_P1.25mm_Vertical
J20: Conn_01x06; Molex_KK-254_AE-6410-06A_1x06_P2.54mm_Vertical
J25: Conn_02x02_Odd_Even; PinHeader_2x02_P2.54mm_Vertical
J30: Conn_01x08; Molex_PicoBlade_53047-0810_1x08_P1.25mm_Vertical
R1, R17, R27: 10k; R_0805_2012Metric_Pad1.20x1.40mm_HandSolder
R2, R12, R13, R14, R37, R38, R39, R40: 1k; R_0805_2012Metric_Pad1.20x1.40mm_HandSolder
R3, R4, R5, R6, R7, R8, R9, R10, R11, R15, R16: 130R; R_0805_2012Metric_Pad1.20x1.40mm_HandSolder
R18, R28: 16k; R_0805_2012Metric_Pad1.20x1.40mm_HandSolder
R19, R29: 51k; R_0805_2012Metric_Pad1.20x1.40mm_HandSolder
R20, R21, R22, R23, R24, R30, R31, R32, R33, R34: 0R; R_0805_2012Metric_Pad1.20x1.40mm_HandSolder
R25, R35: 1M; R_0805_2012Metric_Pad1.20x1.40mm_HandSolder
R26, R36, R47, R49: 0.1R; R_0603_1608Metric_Pad0.98x0.95mm_HandSolder
R48, R50: 0.05 R; R_0603_1608Metric_Pad0.98x0.95mm_HandSolder
SW1: Reset; SW_B3F-1000_OMR
SW2: 5V Bypass; SPDT_OS102011_CNK
SW3: All Power Switch; 26-60-4040_MOL
SW4, SW5, SW6: User_Button; CONN_22232021_MOL
SW7, SW8, SW9, SW10: SW_SPST; CONN_22232021_MOL
U1: PIC32MZ2048EFH144-I/PL; LQFP144_PL_MCH-M
U2, U3: AP2114HA-3.3TRG1; SOT-223_DIO-M
U5, U6, U7, U8: GSF7002DW; SOT-363_SC-70-6
U9: MCP2221A-I_SL; SOIC127P600X175-14N
U10, U13: DRV8842PWPR; PWP0028C_M
U11, U12: Quad_Encoder_Motor; Molex_KK-254_AE-6410-06A_1x06_P2.54mm_Vertical
U15: M95M01-DFMN6TP; SO8N_4X5X1P27_STM-M

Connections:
+3.3V: C2.1, C3.2, C4.2, C5.1, C6.1, C7.2, C8.1, C9.1, C10.2, C13.1, C19.1, C27.1, C28.1, C35.2, C36.2, D11.2 (A), J1.2, J8.1, J13.1, J14.1, J15.1, J17.P4 (VDD), J18.1, J19.5, J22.1, J23.5, J24.5, J26.1, J30.1, J31.1, R1.2, R3.1, R4.1, R5.1, R6.1, R7.1, R8.1, R9.1, R15.1, R16.1, R20.1, R21.1, R22.1, R23.1, R24.1, R30.1, R31.1, R32.1, R33.1, R34.1, SW4.1, SW5.1, SW6.1, SW7.1 (A), SW8.1 (A), SW9.1 (A), SW10.1 (A), U1.18 (VDD), U1.33 (VDD), U1.41 (AVDD), U1.55 (VDD), U1.64 (VDD), U1.88 (VDD), U1.107 (VDD), U1.122 (VDD), U1.137 (VDD), U2.3 (VOUT), U9.1 (VDD), U9.11 (VUSB), U10.16 (RESET_N), U10.17 (SLEEP_N), U11.3 (Vcc), U12.3 (Vcc), U13.16 (RESET_N), U13.17 (SLEEP_N), U15.8 (VCC)
+5V: C11.1, C12.1, C15.1, J3.1, J3.3, J3.5, J3.7, J3.9, SW2.2 (B), SW3.1, U2.1 (VIN), U3.1 (VIN)
/Bump1: R37.1, SW7.2 (B), U1.1 (AN23/RG15)
/Bump2: R38.1, SW8.2 (B), U1.2 (EBIA5/AN34/PMA5/RA5)
/Bump3: R39.1, SW9.2 (B), U1.3 (EBID5/AN17/RPE5/PMD5/RE5)
/Bump4: R40.1, SW10.2 (B), U1.4 (EBID6/AN16/PMD6/RE6)
/Dir1: U1.80 (SCL3/RPF8/RF8), U13.20 (IN2)
/Dir2: U1.117 (EBIA22/RJ3), U10.20 (IN2)
/Fault1: R17.1, U1.9 (EBIBS0/RJ12), U10.18 (FAULT_N)
/Fault2: R27.1, U1.87 (EBIA14/PMCS1/PMA14/RA4), U13.18 (FAULT_N)
/GPS_INT: J24.4, U1.141 (TRD0/SQID0/RG13)
/GPS_Reset: J24.3, U1.142 (EBID2/PMD2/RE2)
/Hold*: U1.60 (AN8/RB13), U15.7 (*HOLD)
/IC1: U1.104 (RPD0/RTCC/INT0/RD0), U11.1 (PhaseA)
/IC2: U1.81 (ERXD0/RH8), U11.2 (PhaseB)
/IC3: U1.6 (EBIA6/AN22/RPC1/PMA6/RC1), U12.1 (PhaseA)
/IC4: U1.13 (EBIOE/AN19/RPC4/PMRD/RC4), U12.2 (PhaseB)
/IMU_INT1: J30.5, U1.112 (EBID12/RPD12/PMD12/RD12)
/IMU_INT2: J30.4, U1.113 (EBID13/PMD13/RD13)
/LED1: U1.66 (AN41/ERXD1/RH5), U5.2 (G1)
/LED2: U1.65 (AN40/ERXERR/RH4), U5.5 (G2)
/LED3: U1.68 (EBIA4/PMA4/RH7), U6.2 (G1)
/LED4: U1.67 (AN42/ERXD2/RH6), U6.5 (G2)
/LED5: U1.72 (OSC2/CLKO/RC15), U7.2 (G1)
/LED6: U1.71 (OSC1/CLKI/RC12), U7.5 (G2)
/MotorCurrent1: R26.2, U1.8 (AN36/ETXD1/RJ9), U10.6 (ISEN), U10.9 (ISEN)
/MotorCurrent2: R36.2, U1.56 (TCK/AN29/RA1), U13.6 (ISEN), U13.9 (ISEN)
/OC1: U1.79 (SDA3/RPF2/RF2), U13.21 (IN1)
/OC2: U1.119 (SQICS1/RPD5/RD5), U10.21 (IN1)
/RA9: J7.1, U1.39 (VREF-/CVREF-/AN27/RA9)
/RA10: J7.2, U1.40 (VREF+/CVREF+/AN28/RA10)
/RB8: J7.7, U1.47 (EBIA10/AN48/RPB8/PMA10/RB8)
/RE1: J25.2, U1.138 (EBID1/PMD1/RE1)
/RE4: J25.1, U1.144 (EBID4/AN18/PMD4/RE4)
/RE7: J16.1, U1.5 (EBID7/AN15/PMD7/RE7)
/RG12: J25.3, U1.140 (TRD1/SQID1/RG12)
/RG14: J25.4, U1.139 (TRD2/SQID2/RG14)
/RH0: J7.3, U1.43 (AN38/ETXD2/RH0)
/RH1: J7.4, U1.44 (AN39/ETXD3/RH1)
/RH2: J7.5, U1.45 (EBIRP/RH2)
/RH3: J7.6, U1.46 (RH3)
/RH12: J21.4, U1.100 (ECRS/RH12)
/RH13: J21.3, U1.101 (ERXDV/ECRSDV/RH13)
/RH14: J21.2, U1.102 (RH14)
/RH15: J21.1, U1.103 (EBIA23/RH15)
/RJ8: J16.2, U1.7 (AN35/ETXD0/RJ8)
/RJ13: J16.3, U1.28 (EBIA13/PMA13/RJ13)
/RJ14: J16.4, U1.29 (EBIA11/PMA11/RJ14)
/RJ15: J16.5, U1.30 (EBIA0/PMA0/RJ15)
/RK1: J7.8, U1.51 (EBIA1/PMA1/RK1)
/RK2: J7.9, U1.52 (EBIA3/PMA3/RK2)
/RK3: J7.10, U1.53 (EBIA17/RK3)
/Refl1: J13.3, U1.50 (AN6/RB11)
/Refl2: J14.3, U1.27 (AN37/ERXCLK/EREFCLK/RJ11)
/Refl3: J15.3, U1.26 (AN4/C1INB/RB4)
/SCK1: J30.7, U1.109 (RPD1/SCK1/RD1)
/SCK2: J20.1, U1.14 (AN14/C1IND/RPG6/SCK2/RG6)
/SCK3: J23.1, U1.61 (AN9/RPB14/SCK3/RB14)
/SCK4: J19.1, U1.98 (RPD10/SCK4/RD10)
/SCK5: U1.57 (TDI/AN30/RPF13/SCK5/RF13), U15.6 (C)
/SCK6: J17.P5 (CLK), U1.70 (AN33/RPD15/SCK6/RD15)
/SCL2: J18.3, U1.85 (SCL2/RA2)
/SDA2: J18.4, U1.86 (EBIRDY1/SDA2/RA3)
/SDI1: J30.8, U1.110 (EBID14/RPD2/PMD14/RD2)
/SDI2: J20.4, U1.15 (AN13/C1INC/RPG7/SDA4/RG7)
/SDI3: J23.3, U1.48 (EBIA7/AN49/RPB9/PMA7/RB9)
/SDI4: J19.3, U1.99 (EMDC/RPD11/RD11)
/SDI5: U1.127 (EBID9/RPG1/PMD9/RG1), U15.2 (Q)
/SDI6: J17.P7 (DAT0), U1.23 (AN25/RPE8/RE8)
/SDO1: J30.6, U1.111 (EBID15/RPD3/PMD15/RD3)
/SDO2: J20.3, U1.16 (AN12/C2IND/RPG8/SCL4/RG8)
/SDO3: J23.4, U1.49 (CVREFOUT/AN5/RPB10/RB10)
/SDO4: J19.4, U1.96 (RPA15/SDA1/RA15)
/SDO5: U1.128 (EBID8/RPG0/PMD8/RG0), U15.5 (D)
/SDO6: J17.P3 (CMD), U1.24 (AN26/RPE9/RE9)
/SS1*: J30.3, U1.118 (SQICS0/RPD4/RD4)
/SS2*: J20.2, U1.21 (EBIA2/AN11/C2INC/RPG9/PMA2/RG9)
/SS3*: J23.2, U1.62 (AN10/RPB15/OCFB/RB15)
/SS4*: J19.2, U1.97 (EBIA15/RPD9/PMCS2/PMA15/RD9)
/SS5*: U1.58 (TDO/AN31/RPF12/RF12), U15.1 (*S)
/SS6*: J17.P2 (CD/DAT3), U1.69 (AN32/RPD14/RD14)
/Status_Green: U1.132 (EBICS1/RJ5), U8.2 (G1)
/Status_Yellow: U1.131 (EBICS0/RJ4), U8.5 (G2)
/Switch1: R14.1, SW6.2, U1.82 (ERXD3/RH9)
/Switch2: R12.1, SW4.2, U1.83 (ECOL/RH10)
/Switch3: R13.1, SW5.2, U1.84 (EBIRDY2/RH11)
/U1RX: U1.90 (EBIA9/RPF4/SDA5/PMA9/RF4), U9.6 (UTX)
/U1TX: U1.91 (EBIA8/RPF5/SCL5/PMA8/RF5), U9.5 (URX)
/U2RX: J24.2, U1.143 (EBID3/RPE3/PMD3/RE3)
/U2TX: J24.1, U1.11 (EBIA12/AN21/RPC2/PMA12/RC2)
/U3RX: J22.4, U1.121 (ETXCLK/RPD7/RD7)
/U3TX: J22.3, U1.120 (ETXEN/RPD6/RD6)
/U4RX: J8.4, U1.37 (PGEC2/AN46/RPB6/RB6)
/U4TX: J8.3, U1.38 (PGED2/AN47/RPB7/RB7)
/U5RX: J26.4, U1.25 (AN45/C1INA/RPB5/RB5)
/U5TX: J26.3, U1.31 (AN3/C2INA/RPB3/RB3)
/U6RX: J31.4, U1.34 (AN2/C2INB/RPB2/RB2)
/U6TX: J31.3, U1.12 (EBIWE/AN20/RPC3/PMWR/RC3)
/USB_RST: U1.92 (EBIA18/RK4), U9.4 (~RST)
/Write Protect*: U1.59 (AN7/RB12), U15.3 (*W)
GND: C1.2, C2.2, C3.1, C4.1, C5.2, C6.2, C7.1, C8.2, C9.2, C10.1, C11.2, C12.2, C13.2, C14.2, C15.2, C19.2, C20.2, C23.2, C24.2, C25.2, C26.2, C27.2, C28.2, C31.2, C32.2, C33.2, C35.1, C36.1, D1.1 (K), J1.3, J2.2, J2.4, J2.6, J2.8, J2.10, J3.2, J3.4, J3.6, J3.8, J3.10, J4.5 (GND), J6.2, J8.2, J9.5 (GND), J13.2, J14.2, J15.2, J16.6, J17.11 (GROUND), J17.12 (GROUND), J17.P6 (VSS), J18.2, J19.6, J20.5, J20.6, J21.5, J21.6, J22.2, J23.6, J24.6, J26.2, J30.2, J31.2, R12.2, R13.2, R14.2, R19.2, R29.2, R37.2, R38.2, R39.2, R40.2, R48.1, R50.1, SW1.1, U1.17 (VSS), U1.32 (VSS), U1.42 (AVSS), U1.54 (VSS), U1.63 (VSS), U1.74 (VUSB3V3), U1.75 (VSS), U1.89 (VSS), U1.108 (VSS), U1.123 (VSS), U1.136 (VSS), U2.2 (GND), U2.4 (GND), U3.2 (GND), U3.4 (GND), U5.1 (S1), U5.4 (S2), U6.1 (S1), U6.4 (S2), U7.1 (S1), U7.4 (S2), U8.1 (S1), U8.4 (S2), U9.14 (VSS), U10.14 (GND), U10.28 (GND), U10.29 (PAD), U11.4 (GND), U12.4 (GND), U13.14 (GND), U13.28 (GND), U13.29 (PAD), U15.4 (VSS)
unnamed: C1.1, R1.1, R2.2, SW1.4
unnamed: D1.2 (A), R3.2
unnamed: D2.2 (A), R4.2
unnamed: D2.1 (K), U5.3 (D2)
unnamed: D3.2 (A), R5.2
unnamed: D3.1 (K), U5.6 (D1)
unnamed: D4.2 (A), R6.2
unnamed: D4.1 (K), U6.3 (D2)
unnamed: D5.2 (A), R7.2
unnamed: D5.1 (K), U6.6 (D1)
unnamed: D6.2 (A), R8.2
unnamed: D6.1 (K), U7.3 (D2)
unnamed: D7.2 (A), R9.2
unnamed: D7.1 (K), U7.6 (D1)
unnamed: D9.2 (A), R15.2
unnamed: D9.1 (K), U9.3 (GP1)
unnamed: D10.2 (A), R16.2
unnamed: D10.1 (K), U9.2 (GP0)
unnamed: D11.1 (K1), R11.2
unnamed: D11.3 (K2), R10.2
unnamed: F1.1, SW3.4
unnamed: J1.1, R2.1, U1.20 (MCLR)
unnamed: J1.4, U1.36 (PGED1/AN0/RPB0/RB0)
unnamed: J1.5, U1.35 (PGEC1/AN1/RPB1/RB1)
unnamed: C14.1, J2.1, J2.3, J2.5, J2.7, J2.9, U3.3 (VOUT)
unnamed: J4.1 (VBUS), SW2.1 (A), SW3.2
unnamed: F1.2, J5.1
unnamed: J5.2, J6.1
unnamed: J9.3 (D+), U9.13 (D+)
unnamed: J9.2 (D-), U9.12 (D-)
unnamed: R18.2, R19.1, U10.12 (VREF), U10.13 (VREF)
unnamed: R26.1, R47.2
unnamed: R28.2, R29.1, U13.12 (VREF), U13.13 (VREF)
unnamed: R36.1, R49.2
unnamed: R47.1, R48.2
unnamed: R49.1, R50.2
unnamed: R10.1, U8.6 (D1)
unnamed: R11.1, U8.3 (D2)
unnamed: C21.1, U10.1 (CP1)
unnamed: C21.2, U10.2 (CP2)
unnamed: R20.2, U10.23 (I0)
unnamed: R21.2, U10.24 (I1)
unnamed: R22.2, U10.25 (I2)
unnamed: R23.2, U10.26 (I3)
unnamed: R24.2, U10.27 (I4)
unnamed: C20.1, R17.2, R18.1, U10.15 (V3P3OUT)
unnamed: C22.2, R25.2, U10.3 (VCP)
unnamed: U11.5 (M+), U13.5 (OUT1), U13.10 (OUT1)
unnamed: U11.6 (M-), U13.7 (OUT2), U13.8 (OUT2)
unnamed: U10.5 (OUT1), U10.10 (OUT1), U12.5 (M+)
unnamed: U10.7 (OUT2), U10.8 (OUT2), U12.6 (M-)
unnamed: C29.1, U13.1 (CP1)
unnamed: C29.2, U13.2 (CP2)
unnamed: R30.2, U13.23 (I0)
unnamed: R31.2, U13.24 (I1)
unnamed: R32.2, U13.25 (I2)
unnamed: R33.2, U13.26 (I3)
unnamed: R34.2, U13.27 (I4)
unnamed: C26.1, R27.2, R28.1, U13.15 (V3P3OUT)
unnamed: C30.1, R35.2, U13.3 (VCP)
Vdrive: C22.1, C23.1, C24.1, C25.1, C30.2, C31.1, C32.1, C33.1, R25.1, R35.1, SW3.3, U10.4 (VM), U10.11 (VM), U13.4 (VM), U13.11 (VM)

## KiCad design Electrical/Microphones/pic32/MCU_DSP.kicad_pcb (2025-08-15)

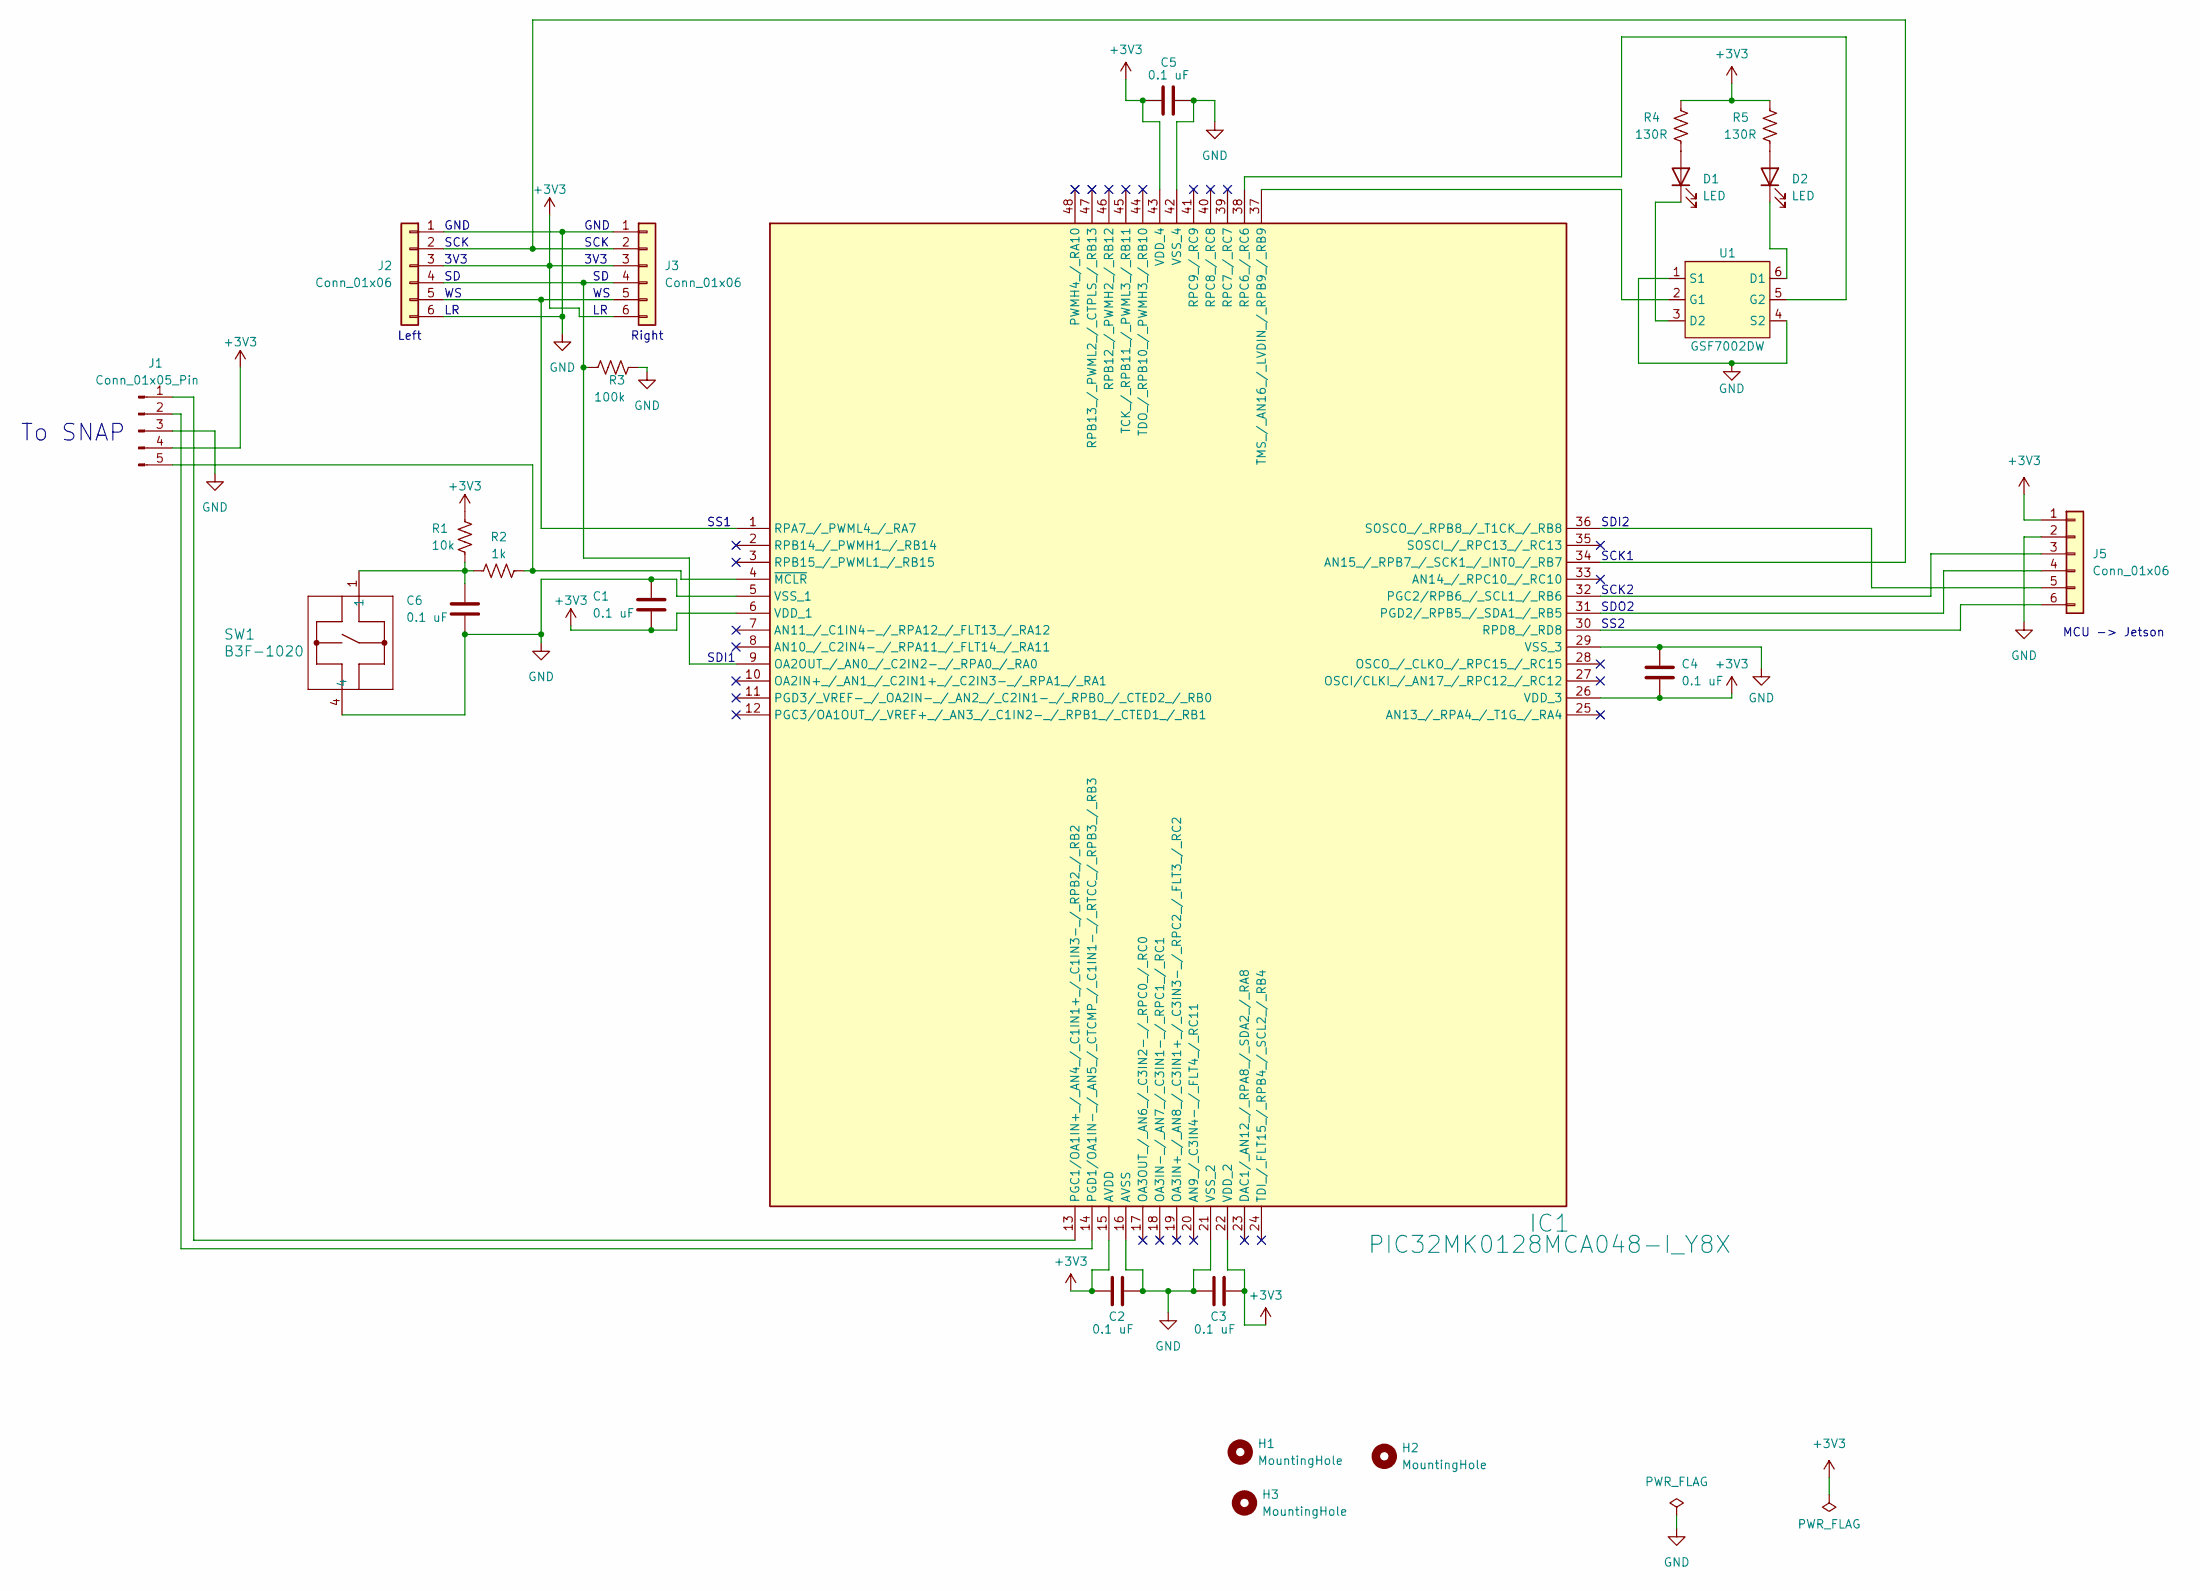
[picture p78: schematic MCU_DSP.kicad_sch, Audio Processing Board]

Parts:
C1, C2, C3, C4, C5, C6: 0.1 uF; C_0805_2012Metric_Pad1.18x1.45mm_HandSolder; Mfr P/N CL21B104KBCNNNC
D1, D2: LED; LED_0805_2012Metric_Pad1.15x1.40mm_HandSolder; Mfr P/N B1701URO-20D000114U1930
H1, H2, H3: MountingHole; MountingHole_3.2mm_M3
IC1: PIC32MK0128MCA048-I_Y8X; TQFP48_Y8X_MCH-M; Mfr P/N PIC32MK0128MCA048T-I/Y8X
J1: Conn_01x05_Pin; PinHeader_1x05_P2.54mm_Horizontal; Mfr P/N 10129379-910002BLF
J2, J3, J5: Conn_01x06; Molex_KK-254_AE-6410-06A_1x06_P2.54mm_Vertical; Mfr P/N 0022232061
R1: 10k; R_0805_2012Metric_Pad1.20x1.40mm_HandSolder; Mfr P/N RMCF0805JT10K0
R2: 1k; R_0805_2012Metric_Pad1.20x1.40mm_HandSolder; Mfr P/N RMCF0805FT1K00
R3: 100k; R_0805_2012Metric_Pad1.20x1.40mm_HandSolder; Mfr P/N RMCF0805FG100K
R4, R5: 130R; R_0805_2012Metric_Pad1.20x1.40mm_HandSolder; Mfr P/N RMCF0805FT130R
SW1: B3F-1020; SW_B3F-1000_OMR; Mfr P/N B3F-1020
U1: GSF7002DW; SOT-363_SC-70-6; Mfr P/N GSF7002DW

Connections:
+3V3: C1.2, C2.1, C3.2, C4.2, C5.2, IC1.6 (VDD_1), IC1.15 (AVDD), IC1.22 (VDD_2), IC1.26 (VDD_3), IC1.43 (VDD_4), J1.4, J2.3, J3.3, J3.6, J5.1, R1.1, R4.1, R5.1
GND: C1.1, C2.2, C3.1, C4.1, C5.1, C6.2, IC1.5 (VSS_1), IC1.16 (AVSS), IC1.21 (VSS_2), IC1.29 (VSS_3), IC1.42 (VSS_4), J1.3, J2.1, J2.6, J3.1, J5.2, R3.2, SW1.4, U1.1 (S1), U1.4 (S2)
unnamed: C6.1, R1.2, R2.1, SW1.1
unnamed: D1.2 (A), R4.2
unnamed: D1.1 (K), U1.3 (D2)
unnamed: D2.2 (A), R5.2
unnamed: D2.1 (K), U1.6 (D1)
unnamed: IC1.34 (AN15_/_RPB7_/_SCK1_/_INT0_/_RB7), J2.2, J3.2
unnamed: IC1.9 (OA2OUT_/_AN0_/_C2IN2-_/_RPA0_/_RA0), J2.4, J3.4, R3.1
unnamed: IC1.13 (PGC1/OA1IN+_/_AN4_/_C1IN1+_/_C1IN3-_/_R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), J1.1
unnamed: IC1.32 (PGC2/RPB6_/_SCL1_/_RB6), J5.3
unnamed: IC1.14 (PGD1/OA1IN-_/_AN5_/_CTCMP_/_C1IN1-_/_RT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), J1.2
unnamed: IC1.31 (PGD2/_RPB5_/_SDA1_/_RB5), J5.4
unnamed: IC1.1 (RPA7_/_PWML4_/_RA7), J2.5, J3.5
unnamed: IC1.38 (RPC6_/_RC6), U1.5 (G2)
unnamed: IC1.30 (RPD8_/_RD8), J5.6
unnamed: IC1.36 (SOSCO_/_RPB8_/_T1CK_/_RB8), J5.5
unnamed: IC1.37 (TMS_/_AN16_/_LVDIN_/_RPB9_/_RB9), U1.2 (G1)
unnamed: IC1.4 (~MCLR), J1.5, R2.2

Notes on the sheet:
SCK
3V3
SS2
GND
MCU -> Jetson
SDO2
SDI2
SCK2
SS1
Left
To SNAP
Right
SDI1
SCK1

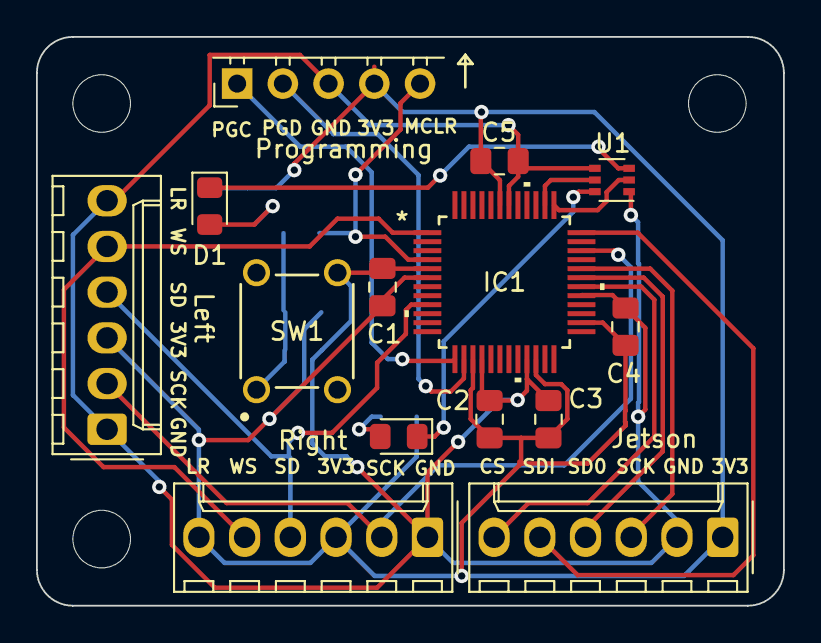
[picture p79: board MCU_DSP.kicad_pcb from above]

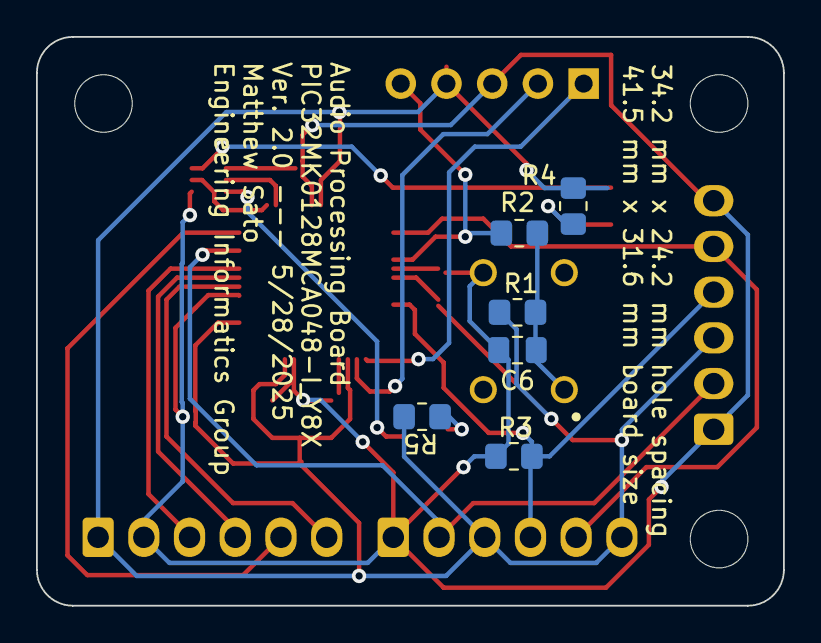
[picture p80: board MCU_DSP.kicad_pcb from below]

Board: 2 copper layers, 41.5 x 31.6 mm, 23 parts (6 on the bottom side), 19 nets.

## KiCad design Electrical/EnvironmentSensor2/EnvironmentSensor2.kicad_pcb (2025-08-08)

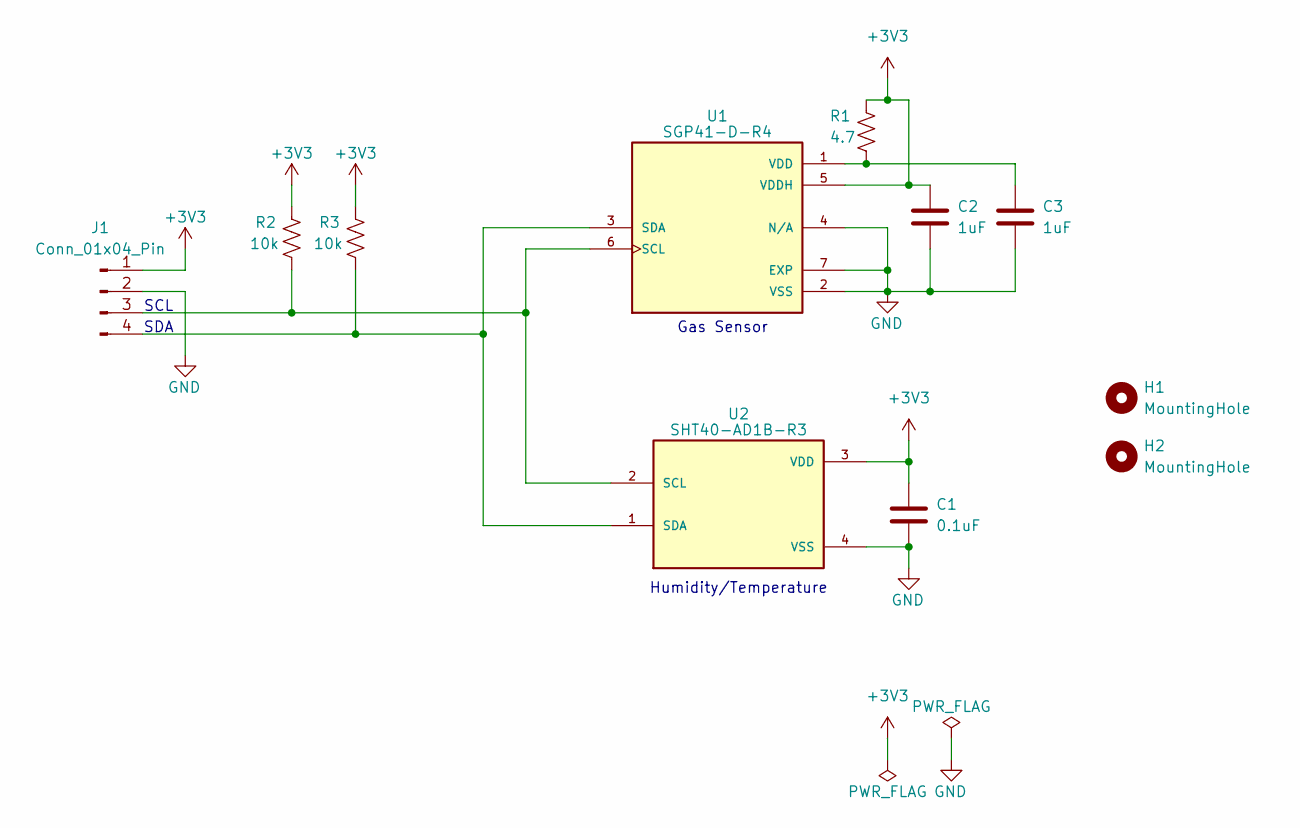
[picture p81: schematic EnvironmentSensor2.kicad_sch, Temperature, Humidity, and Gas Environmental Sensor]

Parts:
C1: 0.1uF; C_0805_2012Metric_Pad1.18x1.45mm_HandSolder; Mfr P/N CL21B104KBCNNNC
C2, C3: 1uF; C_0805_2012Metric_Pad1.18x1.45mm_HandSolder; Mfr P/N 1276-1066-1-ND
H1, H2: MountingHole; MountingHole_3.2mm_M3
J1: Conn_01x04_Pin; Molex_PicoBlade_53048-0410_1x04_P1.25mm_Horizontal; Mfr P/N 0530480410
R1: 4.7; R_0805_2012Metric_Pad1.20x1.40mm_HandSolder; Mfr P/N RC0805FR-074R7L
R2, R3: 10k; R_0805_2012Metric_Pad1.20x1.40mm_HandSolder; Mfr P/N RMCF0805FT10K0
U1: SGP41-D-R4; XDCR_SGP41-D-R4; Mfr P/N SGP41-D-R4
U2: SHT40-AD1B-R3; SHT4X; Mfr P/N SHT40-AD1B-R3

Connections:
+3V3: C1.1, C2.1, J1.1, R1.1, R2.1, R3.1, U1.5 (VDDH), U2.3 (VDD)
GND: C1.2, C2.2, C3.2, J1.2, U1.2 (VSS), U1.4 (N/A), U1.7 (EXP), U2.4 (VSS)
unnamed: J1.3, R2.2, U1.6 (SCL), U2.2 (SCL)
unnamed: J1.4, R3.2, U1.3 (SDA), U2.1 (SDA)
unnamed: C3.1, R1.2, U1.1 (VDD)

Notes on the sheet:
SDA
Gas Sensor
Humidity/Temperature
SCL

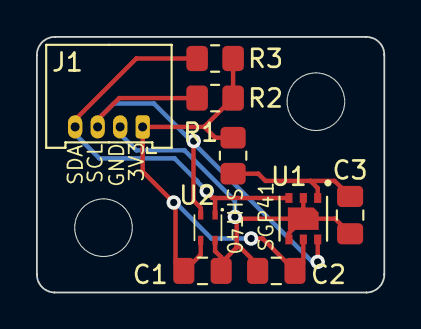
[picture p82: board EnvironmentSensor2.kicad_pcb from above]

Board: 2 copper layers, 19.3 x 14.2 mm, 11 parts (0 on the bottom side), 5 nets.

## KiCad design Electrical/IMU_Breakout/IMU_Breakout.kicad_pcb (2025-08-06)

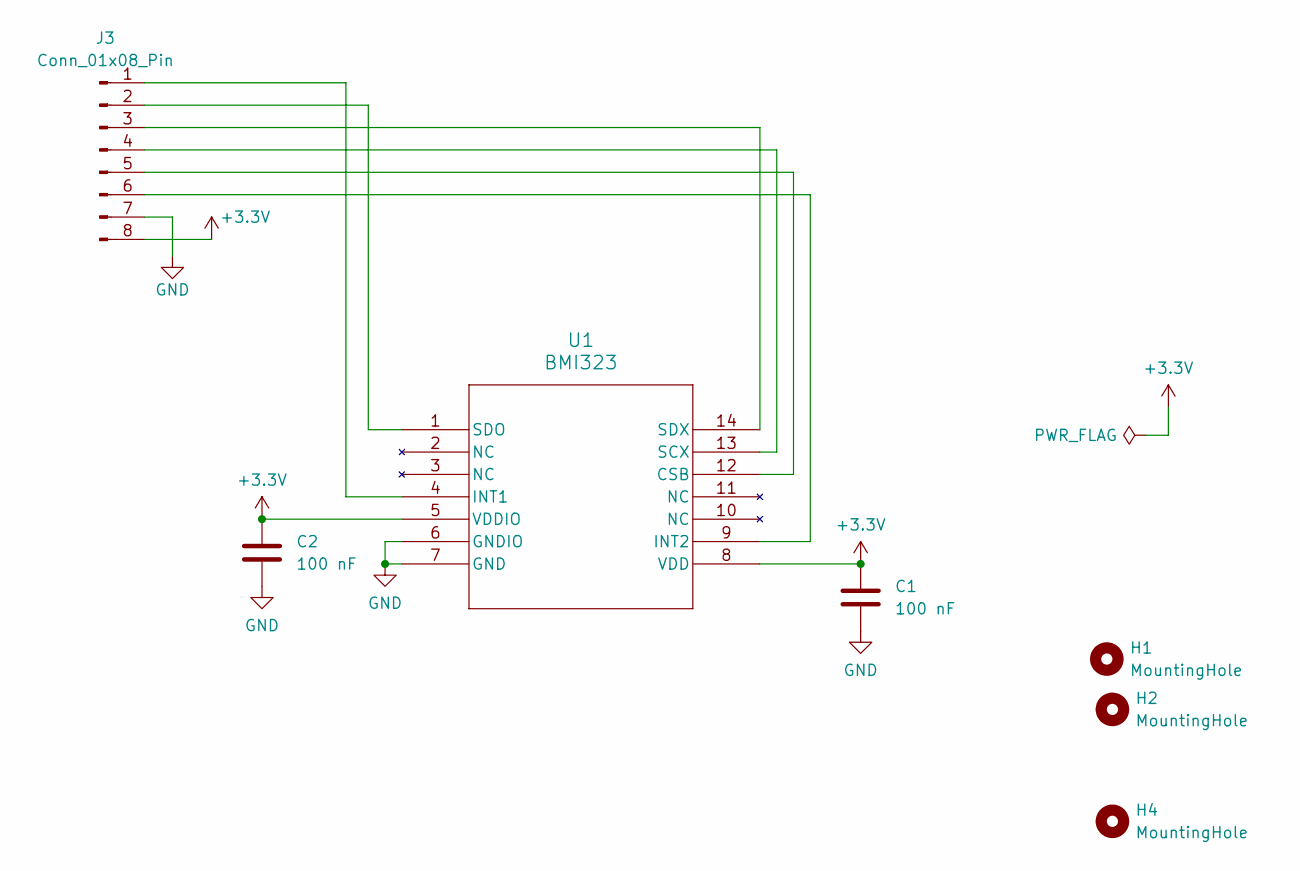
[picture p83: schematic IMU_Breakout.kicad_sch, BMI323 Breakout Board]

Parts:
C1, C2: 100 nF; C_0805_2012Metric_Pad1.18x1.45mm_HandSolder; Mfr P/N CL21B104KBCNNNC
H1, H2, H4: MountingHole; MountingHole_3.2mm_M3
J3: Conn_01x08_Pin; Molex_PicoBlade_53048-0810_1x08_P1.25mm_Horizontal; Mfr P/N 0530480810
U1: BMI323; BMI323_BOS-M; Mfr P/N BMI323

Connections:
+3.3V: C1.1, C2.1, J3.8, U1.5 (VDDIO), U1.8 (VDD)
GND: C1.2, C2.2, J3.7, U1.6 (GNDIO), U1.7 (GND)
unnamed: J3.1, U1.4 (INT1)
unnamed: J3.2, U1.1 (SDO)
unnamed: J3.3, U1.14 (SDX)
unnamed: J3.4, U1.13 (SCX)
unnamed: J3.5, U1.12 (CSB)
unnamed: J3.6, U1.9 (INT2)


Board: 2 copper layers, 26.5 x 23.9 mm, 7 parts (1 on the bottom side), 8 nets.

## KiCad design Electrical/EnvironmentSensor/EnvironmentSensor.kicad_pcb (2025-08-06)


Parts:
C1, C2: 0.1uF; C_0805_2012Metric_Pad1.18x1.45mm_HandSolder; Mfr P/N CL21B104KBCNNNC
H1, H2: MountingHole; MountingHole_3.2mm_M3
IC1: BME690; Mouser Part Number 262-BME690
J1: Conn_01x06_Pin; Molex_PicoBlade_53048-0610_1x06_P1.25mm_Horizontal; Mfr P/N 0530480610

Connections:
unnamed: IC1.2 (CSB), J1.6
unnamed: C1.2, C2.2, IC1.1 (GND_1), IC1.7 (GND_2), J1.2
unnamed: IC1.4 (SCK), J1.5
unnamed: IC1.3 (SDI), J1.4
unnamed: IC1.5 (SDO), J1.3
unnamed: C1.1, C2.1, IC1.6 (VDDIO), IC1.8 (VDD), J1.1

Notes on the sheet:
GND
SDI
CSB
SDO
3V3
SCK


Board: 2 copper layers, 18.3 x 16.7 mm, 6 parts (0 on the bottom side), 6 nets.

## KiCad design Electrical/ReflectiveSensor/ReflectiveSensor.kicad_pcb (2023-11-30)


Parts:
C1: 0.1 uF; C_0805_2012Metric_Pad1.18x1.45mm_HandSolder; Mfr P/N CL21B104KBCNNNC
H1, H2: MountingHole; MountingHole_2.2mm_M2
J1: Refl_Mount; PinHeader_2x02_P2.54mm_Vertical
K1: QRE1113GR; ARUSM-313_100CY_FAS-M; Mfr P/N QRE1113GR
R1: 100R; R_0805_2012Metric_Pad1.20x1.40mm_HandSolder; Mfr P/N RMCF0805FT100R
R2: 10k; R_0805_2012Metric_Pad1.20x1.40mm_HandSolder; Mfr P/N RMCF0805FT10K0

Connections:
unnamed: C1.1, J1.1, R1.2, R2.2
unnamed: C1.2, J1.2, K1.2, K1.4
unnamed: J1.3, K1.3, R2.1
unnamed: K1.1, R1.1

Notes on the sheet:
GND
Sig
3.3V



Board: 2 copper layers, 26.5 x 6.5 mm, 7 parts (3 on the bottom side), 4 nets.

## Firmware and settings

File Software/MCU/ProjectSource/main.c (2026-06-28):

/****************************************************************************
 Module
     main.c
 Description
     starter main() function for Events and Services Framework applications
 Notes

*****************************************************************************/
#include <stdint.h>
#include <stdbool.h>
#include <stdio.h>
#include <assert.h>

#include "ES_Configure.h"
#include "ES_Framework.h"
#include "ES_Port.h"


void main(void)
{
  ES_Return_t ErrorType = Success;

  _HW_PIC32Init(); // basic PIC hardware init
  // Your hardware initialization function calls go here
  
  _PBCLK_Init(); // Set PBLCKs to starting desired frequency

  // now initialize the Events and Services Framework and start it running
  ErrorType = ES_Initialize(ES_Timer_RATE_1mS);
  if (ErrorType == Success)
  {
    _HW_WDT_Reset(); // Check if reset is from WDT
    ErrorType = ES_Run();
  }
  //if we got to here, there was an error
  switch (ErrorType)
  {
    case FailedPost:
    {
      ErrorType = 0; // a hack to get a readable assert message
      assert( FailedPost == ErrorType );
      //DB_printf("Failed on attempt to Post\n");
    }
    break;
    case FailedPointer:
    {
      ErrorType = 0; // a hack to get a readable assert message
      assert( FailedPointer  == ErrorType );
//      DB_printf("Failed on NULL pointer\n");
    }
    break;
    case FailedInit:
    {
      ErrorType = 0; // a hack to get a readable assert message
      assert( FailedInit  == ErrorType );
//      DB_printf("Failed Initialization\n");
    }
    break;
    default:
    {
      ErrorType = 0; // a hack to get a readable assert message
      assert( FailedOther  == ErrorType );
//      DB_printf("Other Failure\n");
    }
    break;
  }
  for ( ; ;)
  {
    ;
  }
}

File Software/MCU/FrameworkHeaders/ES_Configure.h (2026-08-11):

/****************************************************************************
 Module
     ES_Configure.h
 Description
     This file contains macro definitions that are edited by the user to
     adapt the Events and Services framework to a particular application.
 Notes

 History
 When           Who     What/Why
 -------------- ---     --------
 12/19/16 20:19  jec     removed EVENT_CHECK_HEADER definition. This goes with
                         the V2.3 move to a single wrapper for event checking
                         headers
  10/11/15 18:00 jec     added new event type ES_SHORT_TIMEOUT
  10/21/13 20:54 jec     lots of added entries to bring the number of timers
                         and services up to 16 each
 08/06/13 14:10 jec      removed PostKeyFunc stuff since we are moving that
                         functionality out of the framework and putting it
                         explicitly into the event checking functions
 01/15/12 10:03 jec      started coding
*****************************************************************************/

#ifndef ES_CONFIGURE_H
#define ES_CONFIGURE_H

/****************************************************************************/
// Define the Robot ID, this should be a unique 8 bit ID for each robot
#define ROBOT_ID 6

// Define the PCB Revision Number being used
#define PCB_REV 4

// Define which motor type is being used
#define MOTOR_TYPE 1  // The 350RPM motor with 374 pulses per rev
//#define MOTOR_TYPE 2  // The 122RPM motor with 1440 pulses per rev

//#define WHEEL_RADIUS 0.036 // 72 mm wheels
#define WHEEL_RADIUS 0.040 // 80 mm wheels

#define CAR 0
//#define CAR 1 // Car chassis rotated 180 on same wiring (see MotorSM.c)

// H-bridge direction pin level (0 or 1) for robot-forward on each wired channel.
// LATJ3 = wired-left motor, LATF8 = wired-right motor. Flip individually if one
// side drives backward after a mechanical change.
#if CAR
#define HW_LEFT_DIR_FORWARD   1
#define HW_RIGHT_DIR_FORWARD  1
#else
#define HW_LEFT_DIR_FORWARD   0
#define HW_RIGHT_DIR_FORWARD  0
#endif

// Define if we want to log data for RL Motor control
//#define RL_MOTOR_LOGGING

// Set the distance between the wheels
#define WHEEL_BASE 0.258572 // Distance between wheels on the robot (m) (Centered Wheels)
//#define WHEEL_BASE 0.2713 // 122 RPM Car Setup

/****************************************************************************/
// The maximum number of services sets an upper bound on the number of
// services that the framework will handle. Reasonable values are 8 and 16
// corresponding to an 8-bit(uint8_t) and 16-bit(uint16_t) Ready variable size
#define MAX_NUM_SERVICES 16

/****************************************************************************/
// This macro determines that nuber of services that are *actually* used in
// a particular application. It will vary in value from 1 to MAX_NUM_SERVICES
#define NUM_SERVICES 10

/****************************************************************************/
// These are the definitions for Service 0, the lowest priority service.
// Every Events and Services application must have a Service 0. Further
// services are added in numeric sequence (1,2,3,...) with increasing
// priorities
// the header file with the public function prototypes
#define SERV_0_HEADER "UsbService.h"
// the name of the Init function
#define SERV_0_INIT InitUsbService
// the name of the run function
#define SERV_0_RUN RunUsbService
// How big should this services Queue be?
#define SERV_0_QUEUE_SIZE 5

/****************************************************************************/
// The following sections are used to define the parameters for each of the
// services. You only need to fill out as many as the number of services
// defined by NUM_SERVICES
/****************************************************************************/
// These are the definitions for Service 1
#if NUM_SERVICES > 1
// the header file with the public function prototypes
#define SERV_1_HEADER "LEDService.h"
// the name of the Init function
#define SERV_1_INIT InitLEDService
// the name of the run function
#define SERV_1_RUN RunLEDService
// How big should this services Queue be?
#define SERV_1_QUEUE_SIZE 3
#endif

/****************************************************************************/
// These are the definitions for Service 2
#if NUM_SERVICES > 2
// the header file with the public function prototypes
#define SERV_2_HEADER "JetsonSM.h"
// the name of the Init function
#define SERV_2_INIT InitJetsonSM
// the name of the run function
#define SERV_2_RUN RunJetsonSM
// How big should this services Queue be?
#define SERV_2_QUEUE_SIZE 5
#endif
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

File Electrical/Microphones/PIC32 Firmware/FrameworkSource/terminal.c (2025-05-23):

//#define TEST
/****************************************************************************
 Module
   terminal.c

 Revision
   1.0.1

 Description
  File holds functions for printing and receiving characters to/from the serial
  emulator through a UART-USB bridge interface.
 Notes
  For the PIC32 port, we are using UART 1

 History
 When           Who     What/Why
 -------------- ---     --------
 08/29/20 14:46 ram     first pass
 10/05/20 19:38 ram     starting work on PIC32 port
 ***************************************************************************/

/*----------------------------- Include Files -----------------------------*/

// Hardware
#include <xc.h>
#include <stdio.h>

#include "ES_General.h"
#include "ES_Port.h"
#include "circular_buffer.h"
#include "dbprintf.h"

//this module
#include "terminal.h"
/*----------------------------- Module Defines ----------------------------*/
#define BAUD_CONST 129// 42 // sets up baud rate for 115200
//#define BAUD_CONST 21 // sets up baud rate for 230400

/*---------------------------- Module Functions ---------------------------*/
/* prototypes for private functions for this service.They should be functions
   relevant to the behavior of this service
*/

/*---------------------------- Module Variables ---------------------------*/
static uint8_t xmitBuffer[XMIT_BUFFER_SIZE];
static cbuf_handle_t xmitBufferHandle;

/*------------------------------ Module Code ------------------------------*/
/*******************************************************************************
 * Function: TerminalInit
 * Arguments: None
 * Returns nothing
 * 
 * Created by: R. Merchant
 * Description: Sets up UART1 to serve as the terminal interface. Sets the baud
 * rate and maps the needed pins
 ******************************************************************************/
void Terminal_HWInit(void)
{
//#define USE_RB2_3
#ifdef USE_RB2_3
  // This was the original pin choice, though we changed this for the project
  // Set up RB2 as RX and RB3 as TX
  // clear analog control
  ANSELB &= (BIT3LO & BIT2LO);
  // start with TX high
  LATBbits.LATB3 = 1;
  // set RB3 as output
  TRISBbits.TRISB3 = 0;
  // set RB2 as input
  TRISBbits.TRISB2 = 1;
  // Remap the pins
  RPB3R = 0b0001; // U1TX -> RB3
  U1RXR = 0b0100; // U1RX <- RB2
#else
  // this moves the UART pins to RB6 & RB7, freeing up RB2 & RB3 to be used
  // as analog inputs
  ANSELA &= (BIT4LO);  // clear analog control
  LATBbits.LATB4 = 1;           // start with TX high
  TRISBbits.TRISB4 = 0;         // set RB7 as output
  TRISAbits.TRISA4 = 1;         // set RB6 as input
  RPB4R = 0b0001;               // map U1TX -> RB4
  U1RXR = 0b0010;               // map U1RX <- RA4
#endif  //USE_RB2_3
  
  // disable the UART to be safe
  U1MODEbits.ON = 0;
  // Setup high-speed mode, data = 8 bit, no parity, 1 stop bit
  // Disable: loop-back, autobaud, wake, inversion
  U1MODEbits.BRGH = 1;
  // Diable TX inversion, everything else we don't care about
  U1STA = 0;
  // Set the baud rate based on the constant
  U1BRG = BAUD_CONST;
  
  // redirect printf to UART1 using X32 built in cross over
  __XC_UART = 1; 
  
  // enable the UART module
  U1STAbits.UTXEN = 1; // enable transmit 
  U1STAbits.URXEN = 1; // enable receive
  U1MODEbits.ON = 1; // turn peripheral on
  
  // now initialize the circular buffer for transmitting
  xmitBufferHandle = circular_buf_init( xmitBuffer, ARRAY_SIZE(xmitBuffer) );
  
  return;
}
/*******************************************************************************
 * Function: Terminal_ReadByte
 * Arguments: None
 * Returns byte
 * 
 * Created by: R. Merchant
 * Description: Read the byte from the receive register
 ******************************************************************************/
uint8_t Terminal_ReadByte(void)
{
  // wait for there to be something
  while(!(U1STAbits.URXDA))
  {}
  // if there was an overrun, clear it to reset the unit
  if(U1STAbits.OERR) U1STAbits.OERR = 0;
  // return the content of the receive register
  return U1RXREG;
}
/*******************************************************************************
 * Function: Terminal_Write
 * Arguments: byte to write
 * Returns nothing
 * 
 * Created by: R. Merchant
 * Description: Writes the byte to the transmit register or buffer
 ******************************************************************************/
void Terminal_WriteByte(uint8_t txByte)
{
#ifdef NO_BUFFER
  // wait for the register to empty
  while(U1STAbits.UTXBF)
  {}
  // write the byte to the register
  U1TXREG = txByte;
#else
  circular_buf_put(xmitBufferHandle, txByte);
#endif  
  return;
}
/*******************************************************************************
 * Function: Terminal_IsRxData
 * Arguments: none
 * Returns status
 * 
 * Created by: R. Merchant
 * Description: Returns true if there is data in the receive register, or false
 *              if not
 ******************************************************************************/
bool Terminal_IsRxData(void)
{
  
    if(U1STAbits.FERR != 0 ){
        U1RXREG; // in case of a framing error, read the data reg to clear err
        return false;
    }
    // Return Rx Data bit from status register
    return U1STAbits.URXDA;
}

/*******************************************************************************
 * Function: _mon_putc
 * Arguments: char c
 * Returns none
 * 
 * Created by: Ed Carryer
 * Description: this is the function that connects the output of printf() to
 *              hardware. In our case, we are going to use it to stuff the
 *              characters into the circular buffer.
 ******************************************************************************/
void _mon_putc (char c)
{
  circular_buf_put(xmitBufferHandle, c);
}

/*******************************************************************************
 * Function: Terminal_MoveBuffer2UART
 * Arguments: none
 * Returns none
 * 
 * Created by: Ed Carryer
 * Description: this functions pulls bytes, if any available, from the
 *              circular buffer and stuffs them into the UART1 buffer
 *              until we either run out of bytes in the circular buffer
 *              or we run out of space in the UART FIFO
 ******************************************************************************/
void Terminal_MoveBuffer2UART( void )
{
  while ( (!circular_buf_empty(xmitBufferHandle)) && (!U1STAbits.UTXBF))
  {
    uint8_t byte2Xmit;
    circular_buf_get(xmitBufferHandle, &byte2Xmit);
    U1TXREG = byte2Xmit;
  }
}
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

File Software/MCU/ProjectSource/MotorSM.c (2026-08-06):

/****************************************************************************
 Module
   MotorSM.c

 Description
   This is a file for implementing control of the Motors.

 Notes

 History
 When           Who     What/Why
 -------------- ---     --------

****************************************************************************/
/*----------------------------- Include Files -----------------------------*/
/* include header files for this state machine as well as any machines at the
   next lower level in the hierarchy that are sub-machines to this machine
*/
#include "ES_Configure.h"
#include "ES_Framework.h"
#include "MotorSM.h"
#include "LEDService.h"
#include "ADC_HAL.h"
#include "dbprintf.h"
#include <sys/attribs.h>
#include <math.h>
#include "matt_circular_buffer.h"
#include "IMU_SM.h"

/*----------------------------- Module Defines ----------------------------*/
#define IC_PERIOD 65535 // Input capture period
#define OC_PERIOD 200  // 312   // Output compare period (312 ~ 10 kHz, 200==15.625 kHz)
#define NO_SPEED_PERIOD 65535 // Period to indicate motor not spinning
#define DEAD_RECKONING_PERIOD 15624 // Chosen so that we update at 25 Hz rate (50 mHZ / 256 prescaler / 15624 * 2 = 25 Hz)
#define V_PIVOT_THRESH 0.05f // |V_desired| below this with |w_desired| above W_PIVOT_THRESH => pivot gains
#define W_PIVOT_THRESH 0.05f // |w_desired| above this with low V => pivot gains
#define Kp 0.2f // Proportional constant for PID law
#define Ki 0.01f // Integral constant for PID law
#define Kd 0.0f // Derivative constant for PID law
#define CONTROL_PERIOD 30000 // Control update period --- (1000 == 6250*2 Hz, 12500 == 500*2 Hz 30000 == 208*2 Hz)

#define PULSE_LENGTH_ALPHA 0.3f // Exponential Moving average for Pulse Length
#define CONTROL_ALPHA 0.3f // Exponential Moving Average for PID Velocity
#define ODOMETRY_ALPHA 0.3f // Exponential Moving Average for Odometry Velocity

#if (MOTOR_TYPE==1)
#define ENCODER_RESOLUTION (2*374) // Number of pulses per revolution
#elif (MOTOR_TYPE==2)
#define ENCODER_RESOLUTION (1440 / 2) // 720: one ISR per 2 rising edges (ICI=0b01)
#endif

#define SPEED_CONVERSION_FACTOR ((1.25e7*60.0f)/((float)ENCODER_RESOLUTION)) // 1.25e7 = 6.25MHz T3 speed *2

#define DEAD_RECKONING_TIME (256.0f  * DEAD_RECKONING_PERIOD / 2.0f / 50000000.0f) // Time between dead reckoning updates in seconds (depends on DEAD_RECKONING_PERIOD)
#define DEAD_RECKONING_RATIO (2.0f * (float)M_PI / ENCODER_RESOLUTION / DEAD_RECKONING_TIME * WHEEL_RADIUS) // This number times change in encoder clicks is linear velocity in m/second
#define CONTROL_TIME (8.0f * CONTROL_PERIOD / 2.0f / 50000000.0f)
#define CONTROL_RATIO (60.0f / ENCODER_RESOLUTION / CONTROL_TIME) // This number times change in encoder clicks is rpm
#define HYBRID_COUNT_ENTER_DELTA 4 // Switch to count-based RPM when |delta| > 3
#define HYBRID_COUNT_EXIT_DELTA  2 // Return to pulse-length RPM when |delta| <= 2

#define V_MAX 1 // max 1 m/sec
#define w_MAX 3 // max 2 rad/sec

/* PWM slew: ~600 ms; also used for soft-stop and reverse-through-zero */
#define DUTY_RAMP_TIME_S   0.25f
#define T1_CONTROL_DT_S    ((8.0f * (float)CONTROL_PERIOD) / 2.0f / 50000000.0f) /* matches T1 1:8, PR1 */
#define DUTY_SLEW_MAX_PCT  (100.0f * T1_CONTROL_DT_S / DUTY_RAMP_TIME_S)
#define DUTY_STOP_EPS_PCT  1.0f
#define RPM_REVERSE_EPS    10.0f /* flip H-bridge only once wheels are nearly stopped */
#define RPM_SLEW_MAX       (200.0f * T1_CONTROL_DT_S / DUTY_RAMP_TIME_S) /* soft RPM setpoint after reverse */
#define I_FOLDBACK_MA      2000 /* duty foldback above 2.0 A; stall peaks observed >2.2 A */

// Encoder stall: commanded motion but no wheel speed → cut PWM (complements ISEN foldback) 
// Detect: all of Desired>min, AppliedDuty>min, Actual<max, dirs match, past grace, for TIME_S 
#define STALL_RPM_MAX          8.0f   // ActualRPM below this = "not moving" (detect); above = motion recovered
#define STALL_DESIRED_MIN     20.0f   // DesiredRPM must exceed this to arm detect; drop below to clear latch
#define STALL_DUTY_MIN         8.0f   // AppliedDuty % must exceed this so we only trip when actually driving
#define STALL_TIME_S           0.25f  // How long the detect conditions must hold before latching
#define STALL_GRACE_S          0.15f  // Ignore detect this long after DesiredRPM rises above DESIRED_MIN (takeoff)
#define STALL_CLEAR_RPM_TICKS  3      // Consecutive ticks with ActualRPM > RPM_MAX before clearing latch

#define BUFF_SIZE 65

#if (PCB_REV <= 2)
#define ENCODER_SIGN ((1)*(CAR ? -1 : 1)) // Flip the sign of the encoder readings for the car chassis
#else
#define ENCODER_SIGN ((-1)*(CAR ? -1 : 1)) // Flip the sign of the encoder readings for the car chassis
#endif
/*---------------------------- Module Functions ---------------------------*/
/* prototypes for private functions for this machine.They should be functions
   relevant to the behavior of this state machine
*/
static void Store_RL_Data(void);
static bool IsPivotControlMode(void);
static int8_t EncoderDeltaFromEdge(uint8_t RisingEdge, uint8_t ChannelB);
static uint16_t ReadSecondCapture(volatile uint32_t *icbuf);
static void SetMotorDirection(bool LeftDir, bool RightDir);
static float SlewToward(float applied, float target, float max_delta);
static float SlewDuty(float applied, float target);
static void WriteMotorDuty(float left_pct, float right_pct, bool left_dir, bool right_dir);
static bool UpdateStallLatch(bool *latched, float *timer, float *grace, float *prev_des,
                             bool *dir_at_latch, uint8_t *clear_rpm_ticks,
                             float desired, float actual, float applied,
                             bool cmd_dir, bool applied_dir,
                             bool *rpm_soft_start, float *cmd_rpm);

/*---------------------------- Module Variables ---------------------------*/
// everybody needs a state variable, you may need others as well.
// type of state variable should match that of enum in header file
static MotorState_t CurrentState;

// Everything we need for measuring motor speed
static volatile MotorTimer_t MyTimer;
static volatile uint32_t * pLeftPulseLength; 
static volatile uint32_t * pRightPulseLength;
static volatile uint32_t IC1PulseLength = 4294967295;
static volatile uint32_t IC3PulseLength = 4294967295;
static volatile uint32_t IC1PrevTime = 0;
static volatile uint32_t IC3PrevTime = 0;

// Used for dead reckoning to determine current position
static volatile int32_t * pLeftRotations;
static volatile int32_t * pRightRotations;
static volatile int32_t LeftPrevRotations = 0;
static volatile int32_t RightPrevRotations = 0;
static volatile int32_t IC1Rotations = 0;
static volatile int32_t IC3Rotations = 0;

// Variables for odometry calculation
static volatile float x = 0; // x position of the robot
static volatile float y = 0; // y position of the robot
static volatile float theta = 0; // angular position of the robot
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

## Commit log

2023-11-08 Add initial directories and READMEs
    [MainBoard.kicad_pcb, MainBoard.kicad_sch]
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2023-11-11 Add the majority of the electronics
    [10118193-0001LF.step, 22232021.stp, 4628.step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]
2023-11-12 Add more schematics and begin floorplanning
    [GPIO.kicad_sch, IMU.kicad_sch, LED.kicad_sch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]
2023-11-13 Begin layout of pcb
    [APAE1590R2540AKDB1-T.step, Buttons.kicad_sch, GPIO.kicad_sch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]
2023-11-16 First Pass at the routing
    [GPIO.kicad_sch, GPS.kicad_sch, MainBoard.kicad_pcb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]
2023-11-25 Add some finishing touches and create preliminary boms
    [GPIO.kicad_sch, GPS.kicad_sch, IMU.kicad_sch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]
2023-11-25 Some finishing touches to the board
    [022232031.stp, 022232041.stp, 026604040.stp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]
2023-11-25 Add a bom and initial mechanical drawings
    [BOM.xlsx]
2023-11-25 Move reflectlive sensors to own schematic
    [MainBoard-B_Cu.gbr, MainBoard-B_Mask.gbr, MainBoard-B_Paste.gbr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]
2023-11-25 Finalize Reflective Opto Sensor
    [DigiKey_BOM.xlsx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]
2023-11-26 Add some final touches
    [MainBoard-B_Cu.gbr, MainBoard-B_Mask.gbr, MainBoard-B_Paste.gbr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]
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2023-11-27 Resize the reflective sensor
    [ReflectiveSensor.kicad_pcb, ReflectiveSensor.kicad_sch]
2023-11-27 Add updated robot design
    [2_inch_hex_standoff.SLDPRT, 3_inch_hex_standoff.SLDPRT, 8_inch_hex_standoff.SLDPRT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]
2023-11-28 Update the main power switch
    [MainBoard.kicad_pcb, Power.kicad_sch, bom_digikey_PIC32_1.xlsx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]
2023-11-30 Finish final board design for Rev 0.1 Main board and reflective Sensor. Created Gerbers.
    [GPIO.kicad_sch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]
2023-11-30 Create archive folder to keep track of revisions
    [022232031.stp, 022232041.stp, 026604040.stp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]
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2023-12-29 Add comments to schematic for future revs
    [IMU.kicad_sch, Motor.kicad_sch]
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2024-01-11 Made a comment that we may need a small resistor to draw some current from battery to keep on
    [Power.kicad_sch]
2024-01-15 Add updated mechanical drawings
    [LED.sldprt, NiMH_battery.SLDPRT, control_panel.DXF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]
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2024-01-20 Add updated stl files
    [3_inch_hex_standoff.SLDPRT, ball_caster.SLDPRT, drive_shaft.SLDPRT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]
2024-01-23 Move pillow blocks closer to wheel holes
    [control_panel.DXF, control_panel.SLDPRT, drive_shaft.SLDPRT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]
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2024-01-26 Get most services at least functioning without crashing
    [ES_Configure.h, JetsonSM.c]
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2024-01-29 Updates to robot upper level design
    [6_inch_cir_standoff.SLDPRT, 6_inch_cir_standoff.STL, A2_LIDAR.SLDPRT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]
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2024-02-02 Add IMU breakout board design
    [BMI323_BOS.step, IMU_Breakout.kicad_pcb, IMU_Breakout.kicad_sch]
2024-02-02 Made V0.2 revisions to Main Board
    [Buttons.kicad_sch, GPIO.kicad_sch, GPS.kicad_sch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]
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2024-02-07 Change molex+terminal block to just 6 position molex for the motor/encoder terminal
    [MainBoard.kicad_pcb, Motor.kicad_sch]
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2024-02-07 Add holes for IMU, batteryholder
    [12V_Battery.SLDPRT, IMU breakout.SLDPRT, NiMH_holder.SLDPRT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]
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2024-02-14 Change some spi stuff with jetson, probably will need to revert
    [JetsonSM.c, MotorSM.c]
2024-02-14 Revert "Change some spi stuff with jetson, probably will need to revert"
    This reverts commit 06b93681a91bff43f5faf43f78ca409b5d33d08e.
    Revert back to PI control instead of PID
    [JetsonSM.c, MotorSM.c]
2024-02-14 Revert "Update motor PID paramters, need to figure out overflow of Jetson SPI"
    This reverts commit 0b59fb96bbd7ab252bd332ff9b5508b7fe41d7a4.
    Reverting back to PI control instead of PID
    [JetsonSM.c, MotorSM.c, UsbService.c]
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2024-02-14 Allocate 16 bytes for the receiveBuffer-- May have been causing the problem of data getting misaligned with jetson
    [JetsonSM.c]
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2024-03-10 Finalize IMU Breakout board
    [IMU_Breakout-B_Cu.gbr, IMU_Breakout-B_Mask.gbr, IMU_Breakout-B_Paste.gbr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]
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2024-03-10 Add V0.2 to archive
    [022232031.stp, 022232041.stp, 026604040.stp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]
2024-03-20 Add updated mechanical details for new motor
    [12V_Battery.SLDPRT, 2_inch_hex_standoff.SLDPRT, 3_inch_hex_standoff.SLDPRT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]
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2024-04-02 Add updated dxf/stl files for new motor
    [12V_Battery.SLDPRT, 2_inch_hex_standoff.SLDPRT, 3_inch_hex_standoff.SLDPRT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]
2024-04-02 Finalize code for setting up IMU and verifying soldering is correct
    [IMU_SM.c]
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2024-05-03 Make a note on future revision needs
    [Buttons.kicad_sch, GPIO.kicad_sch, GPS.kicad_sch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]
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2024-08-19 Reduce control frequency for motor to not have issues with Jetson. Also, for V0.2 PCB only do IC every 4 to reduce amount of captures
    [JetsonSM.c, MotorSM.c]
2024-08-20 Tune parameters in Motor and fix small issues
    [MotorSM.c]
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2025-05-15 Update mechanical, begin readme
    [12V_Battery.SLDPRT, 2_inch_hex_standoff.SLDPRT, 3_inch_hex_standoff.SLDPRT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]
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2025-05-19 Fix SPI3 and make visual improvements
    [Buttons.kicad_sch, GPIO.kicad_sch, GPS.kicad_sch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]
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2025-06-03 Fix the wrong timers being used for not encoder reading stopped
    [MotorSM.c]
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2025-06-09 Add mechanism for resetting errorsum and prev error in ISR when robot is commanded to be static
    [MotorSM.c]
2025-06-09 Add code to ignore wrong RPM Measurements
    [ES_Configure.h, MotorSM.c]
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2025-06-13 Update STLs for 7 mm board thickness and 80 mm wheel
    [3.5_inch_cir_standoff.STL, 3.5inch_standoff.0001.ipt, 3.5inch_standoff.0002.ipt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]
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2025-06-18 Indicate the parts that can be 3D printed no matter the materials purchased
    [3d_print.xlsx]
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2025-06-18 Add details about bearing block with flanged vs non flanged bearings
    [3d_print.xlsx, wheel_bearing_block_no_flange.stl, wheel_bearing_no_flange.0001.ipt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]
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2025-06-23 Update previews and provide information of print length and settings
    [layer1_car.dxf, level1.DXF, mobile_robot_car.0065.iam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]
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2025-07-01 Update the layer 1 for new ball caster location
    [layer1_new.0030.ipt, layer1_new.0032.ipt, layer1_new.ipt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]
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2025-07-05 Do not allow too large of measured V or w
    [MotorSM.c]
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2025-07-21 fix level 3 hole size for standoffs
    [layer3_new.0005.ipt, layer3_new.0006.ipt, layer3_new.ipt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]
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2025-08-06 Add more lines for aligning imu when soldering
    [EnvironmentSensor.kicad_pcb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]
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2025-08-06 Change some connections to picoblade, add env sensor connector
    [530470610.stp, 530470810.stp, Buttons.kicad_sch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]
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2025-08-08 Add environmental sensor which uses separate temp/hum and gas sensors (more open source)
    [530480410.stp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]
2025-08-08 Use more molex picoblades and make schematic prettier
    [530470410.stp, Buttons.kicad_sch, GPS.kicad_sch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]
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2025-08-15 Make a robot assembly with all round layers
    [layer2.0006.ipt, layer2.ipt, layers3-6.iam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]
2025-10-01 Modify astra holder for better fit and easier 3D printing
    [astra_holder.0005.ipt, astra_holder.0007.ipt, astra_holder.STL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]
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2025-10-01 Modify circular layers 1 and 2 for larger standoff hole sizes
    [layer1.0003.ipt, layer1.0005.ipt, layer1.ipt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]
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2025-10-19 Fix SPI reception handling to prevent message loss when data is delayed
    [JetsonSM.c]
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2026-05-16 Update the control timer frequency to 1000 (previously missing factor of 2)
    [MotorSM.c]
2026-05-16 Fix comments and correct SPI2 configuration in Jetson state machine
    [JetsonSM.c]
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2026-05-17 Fix indexing in messsage to send
    [IMU_SM.c]
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2026-05-22 Enhance IMU state machine: add IMURecovering state, implement recovery logic, and improve error handling
    [IMU_SM.c]
2026-05-22 Refactor IMU and Motor state machine: adjust interrupt priorities, enhance angle computation logic, and improve pitch correction based on IMU state
    [IMU_SM.c, MotorSM.c]
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2026-05-24 Fix small bugs and add hysteris for rpm calculation in motor control
    [MotorSM.c]
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2026-06-27 Enable backup motor brownout to stop motors and reset jetson connection
    [ES_Configure.h, MotorSM.c]
2026-06-28 Add WDT Reset (0.5 s) when software is stuck somewhere
    [ES_Configure.h, ES_Port.c, UsbService.c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]
